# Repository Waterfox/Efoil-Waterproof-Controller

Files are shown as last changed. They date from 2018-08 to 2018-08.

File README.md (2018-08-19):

# Efoil-Waterproof-Controller

This repository contains everything you should need to build a waterproof controller for your electric hydrofoil

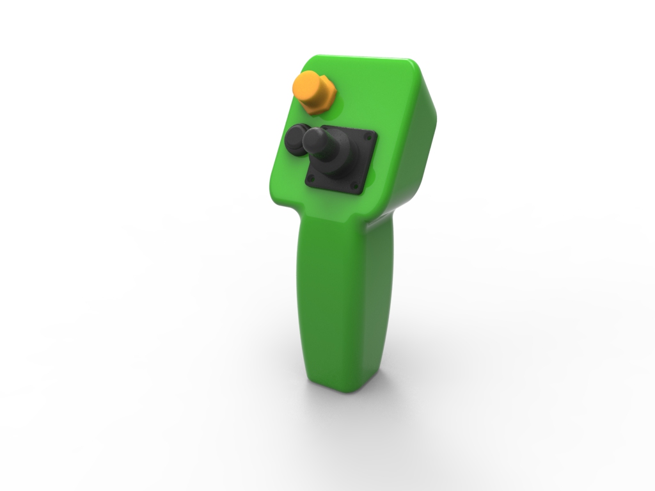
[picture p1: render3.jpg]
Controller Render


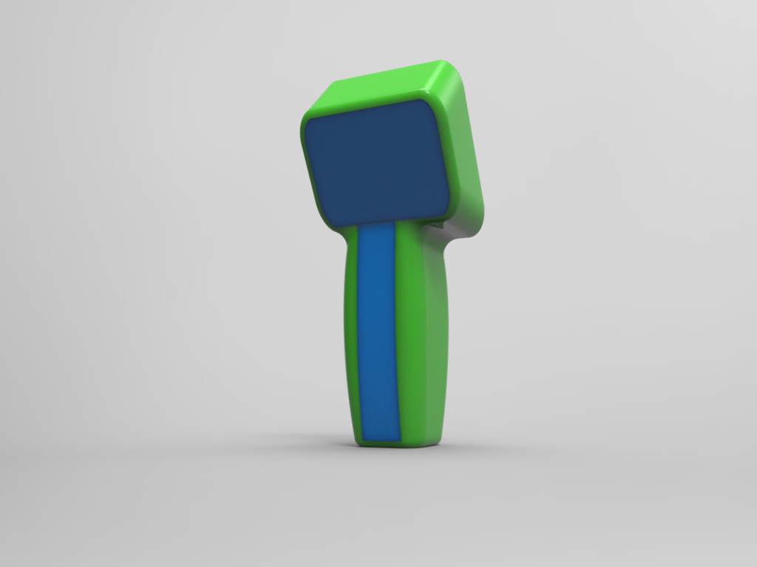
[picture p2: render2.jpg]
Controller Render


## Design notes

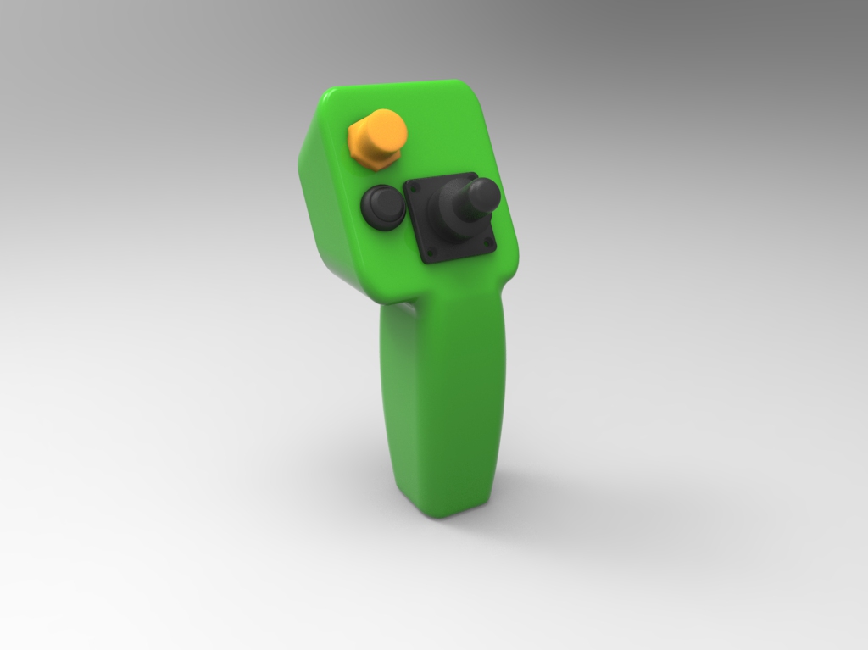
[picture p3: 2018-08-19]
render1.jpg

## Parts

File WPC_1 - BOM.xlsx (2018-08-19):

# | Part | Description | Manufacturer | Part number | Supplier | Supplier # | Quantity | Unit | CUR | Extended Cost | Website
1 | Joystick IP67 | SWITCH JOYSTICK FINGER TIP HALL | Grayhill | 67A-DF-3C-060C | Digikey | GH7700-ND (https://www.digikey.ca/product-detail/en/grayhill-inc/67A-DF-3C-060C/GH7700-ND/4360140) | 1 | 89 | CAD
2 | RF module - RX | SPARKFUN TRANSCEIVER BREAKOUT - SMA | Sparkfun | WRL-00705 | Digikey | 1568-1296-ND (https://www.digikey.ca/product-detail/en/sparkfun-electronics/WRL-00705/1568-1296-ND/5762446) | 1 | 28.41 | CAD
3 | RF module - TX | SPARKFUN TRANSCEIVER BREAKOUT - | Sparkfun | WRL-00691 | Digikey | 1568-1295-ND (https://www.digikey.ca/product-detail/en/sparkfun-electronics/WRL-00691/1568-1295-ND/5762445) | 1 | 28.41 | CAD
4 | Battery charger | SPARKFUN USB LIPOLY CHARGER - SI | Sparkfun | PRT-12711 | Digikey | 1568-1299-ND (https://www.digikey.ca/product-detail/en/sparkfun-electronics/PRT-12711/1568-1299-ND/5762449) | 1 | 21.29 | CAD
5 | Teensy MCU | DEV TEENSY 3.2 13736 | PJRC | DEV-13736 | Digikey | 1568-1231-ND | 2 | 31.6 | CAD
6 | ON/OFF but | SWITCH PUSHBUTTON SPST 4A 12V | APEM | IPR1SAD2L0G | Digikey | 679-1115-ND | 1 | 40.36 | CAD
7 | Charge port | Chogori Standard Series 4 POS Panel | Chogori | 22004535-01 |  |  |  |  |  |  | http://www.chogoriusa.com/standard.pdf
8 | Charge plug | Chogori Standard Series 4 POS Push Lock, Field installable | Chogori | 22004231-01
9 | USB A cable | USB A Cable
10 | 2 Part Urethane | Smooth-ON PMC 780 2 part Urethane |  |  |  |  |  |  |  |  | https://www.smooth-on.com/products/pmc-780-dry/
11 | Resistor 2K | I2C pullups, 2K-5K |  |  |  |  | 2
12 | Resistor 100 | Button LED, 100 Ohm |  |  |  |  | 1
13 | Battery | 1 cell from a Turnigy 3S 2200mAh LiPO | Hobbyking |  | HobbyKing | T2200.3S.20 | 1 | 8 | USD |  | https://hobbyking.com/en_us/turnigy-2200mah-3s-20c-lipo-pack.html
14 | M3 Screws | M3 X 5MM SHCS 18-8SS
15 | 5V reg | Regulate from your battery volage to 5V
WPC01 | 3D printed enclosure
WPC02 | 3D printed back panel 1
WPC03 | 3D printed back panel 2
WPC04 | controller assy

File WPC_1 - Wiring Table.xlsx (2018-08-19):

Waterproof Controller Basic Wiring
Waterproof Controller:
Teensy | NRF24L01 | Note
VIN | VCC | 4.2V from LIPO
GND | GND
D8 | IRQ
D9 | CE
D10 | CS
D11 | MOSI
D12 | MISO
D13 | SCK
 | Grayhill 67A
18 - SDA0 | 1 - SDA | Use pullup R to VIN or 3V3
3.3V | 2 - VDD
GND | 3 - VSS | GND
19 - SCL0 | 4 - SCL | Use pullup R to VIN or 3V3
D7 | 5 - INTn | connected but not used
 | 6 - A1n
 | Chogori Panel Connector
 | 1 | 5V Input from USB Charger
D- Pad | 2 | White wire USB
D+ Pad | 3 | Green wire USB
 | 4 | GND from USB Charger
 | Other
VIN | Pushbutton Switch from SF LiPo charger output
GND | SF LiPO charger output
Receiver:
Teensy | NRF24L01
VIN | VCC
GND | GND
D8 | IRQ
D9 | CE
D10 | CS
D11 | MOSI
D12 | MISO
D13 | SCK
 | Seaking 130A ESC
GND | BLACK
VIN | RED
D3 | White
 | 5V Reg
VIN | 5V REG '+ve'
GND | 5V REG GND

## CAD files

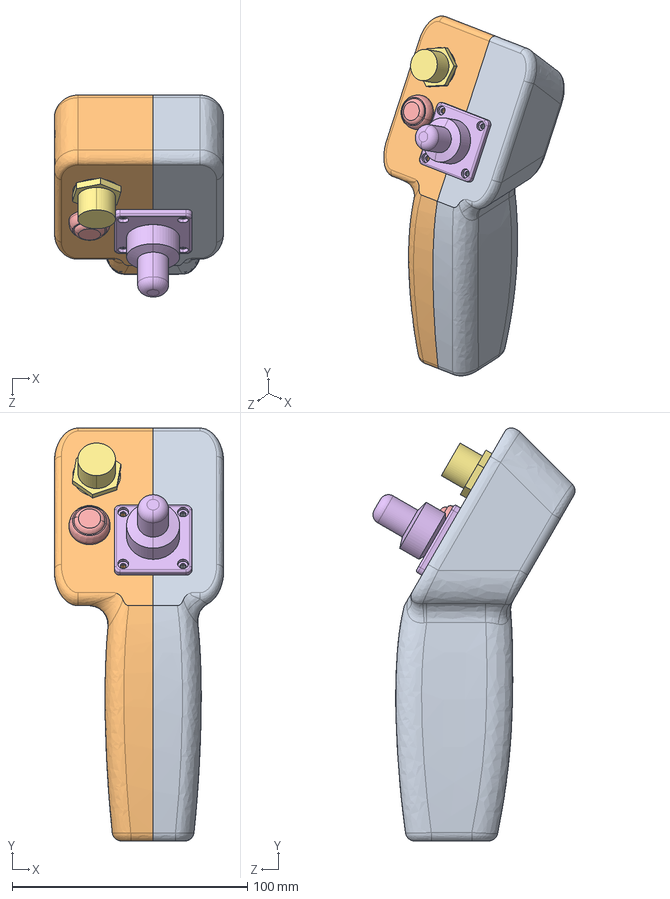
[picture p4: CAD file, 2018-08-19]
WPC04 - controller assy.STEP
72.0 x 175.4 x 85.8 mm
WPC01 - enclosure
2.6LipoFP
teensyFP
ApemPushbutton
grayhill67A
chogori fp
WPC03 - back cover2
WPC02 - back cover1

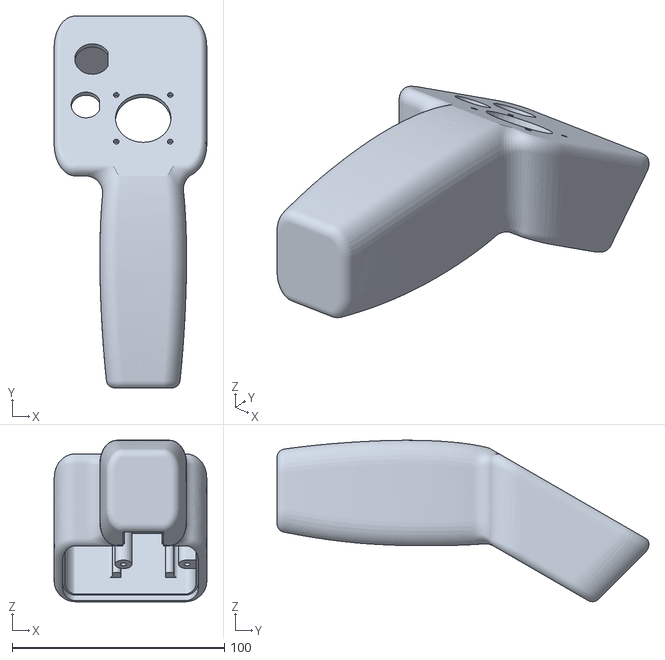
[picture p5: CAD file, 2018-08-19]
WPC01 - enclosure.STL
72.0 x 175.4 x 76.2

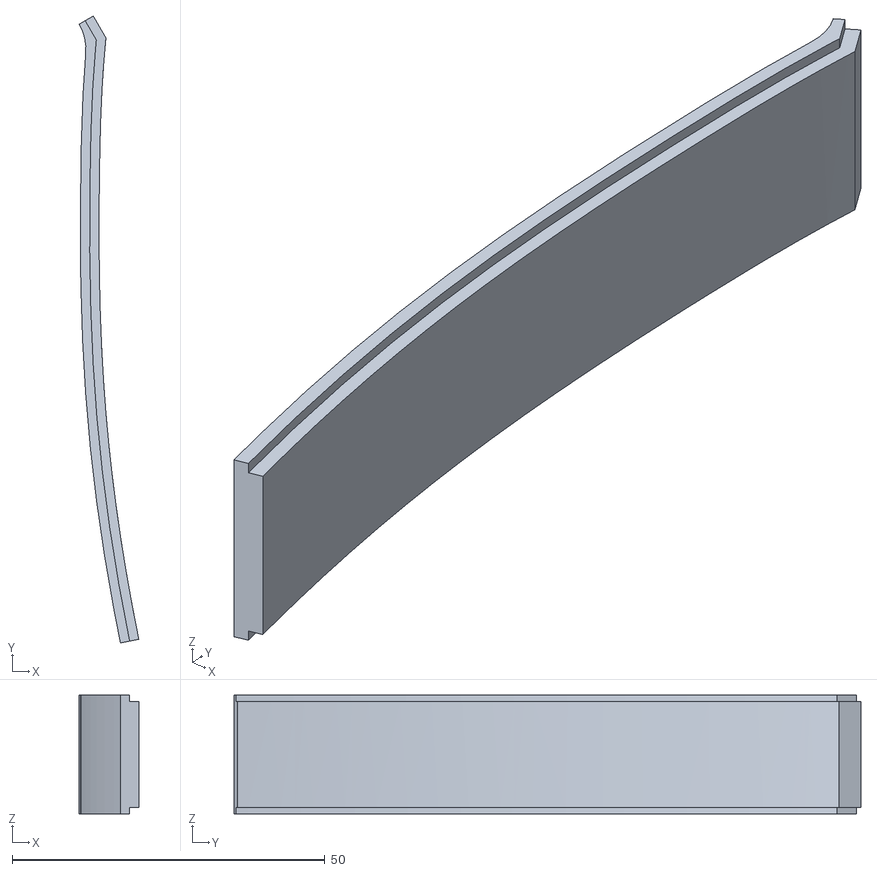
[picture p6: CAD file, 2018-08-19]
WPC03 - back cover2.STL
9.54 x 100.3 x 19.0

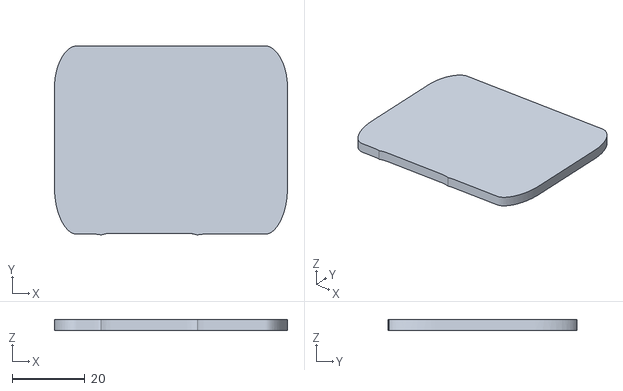
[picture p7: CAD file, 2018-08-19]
WPC02 - back cover1.STL
64.0 x 51.9 x 3.00

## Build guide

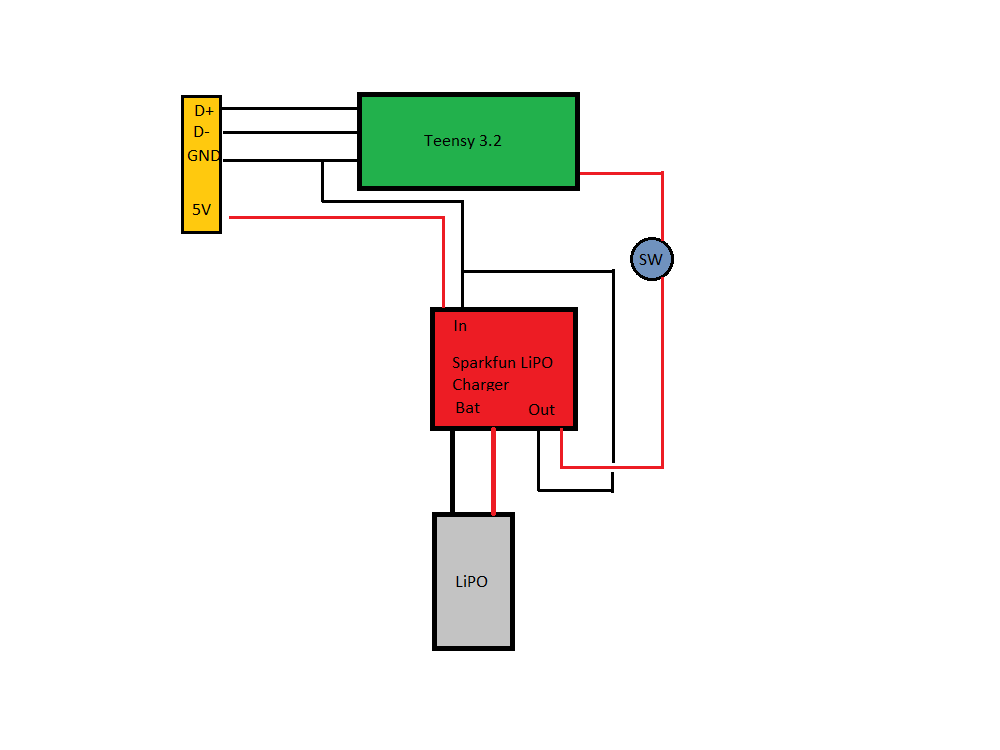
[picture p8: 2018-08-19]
bat charger wiring.png

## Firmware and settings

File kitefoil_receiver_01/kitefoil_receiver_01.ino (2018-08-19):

/* 
*  Wireless remote controller receiver with Grayhill 67A joystick and nRF24L01+ radios
*  Based on Teensy Examples
*  July 2018 Robbie Edwards
*/

#include <SPI.h>
#include <RF24.h>
#include <Servo.h>
#define THRUSTER_PIN 3

RF24 radio(9,10);
int xy[] = {0,0};
Servo m1;
int thruster_out = 90;
int missCount = 11;

byte addresses[][6] = {"1Node","2Node"};

void setup() {
  Serial.begin(115200);
  m1.attach(THRUSTER_PIN);
  radio.begin();
//  radio.setPALevel(RF_PA_LOW);
  radio.openReadingPipe(1,addresses[1]);
  radio.startListening();

}

void loop() {
  if (missCount > 10) thruster_out = 90; // If we don't receive anything for 10 cycles, set throttle to neutral
  if( radio.available()){
                                                                    
      while (radio.available()) {                                   
        radio.read( &xy, sizeof(xy) );             
      }
     
      Serial.print(xy[0]);Serial.print("  "); Serial.println(xy[1]);
      thruster_out = map(xy[1],-80,80,8,172);  // map the joystick output to the servo range
      missCount = 0;
   }
   else missCount = missCount + 1;

   if (thruster_out < 90) thruster_out = 90; // Don't allow reverse
   m1.write(thruster_out);
   delay(20);
}

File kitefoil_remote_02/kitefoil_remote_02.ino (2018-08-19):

/* 
*  Wireless remote controller with Grayhill 67A joystick and nRF24L01+ radios
*  Based on Teensy Examples
*  July 2018 Robbie Edwards
*/

#include <Wire.h>
#include <SPI.h>
#include <RF24.h>

//int led = LED_BUILTIN;
int x = 0;
int y = 0;
int xy[] = {0,0};

RF24 radio(9,10);
byte addresses[][6] = {"1Node","2Node"};

void setup()
{
//  pinMode(led, OUTPUT);
  Wire.begin();             // join i2c bus 
  Serial.begin(115200);       // start serial for output

  radio.begin();
//  radio.setPALevel(RF_PA_LOW);
  radio.openWritingPipe(addresses[1]);
  radio.openReadingPipe(1,addresses[0]);
  
}

void loop()
{


//  digitalWrite(led, HIGH);  // briefly flash the LED
  //Read from the Grayhill 67A Joystick
  xy[0] = 0;
  xy[1] = 0;
  Wire.requestFrom(0x40, 2);   // 7 bit address, the read / write bit is appended by Wire lib
  if (Wire.available()) { // slave may send less than requested
    int c = Wire.read();   // receive a byte as character
    if (c >127) xy[0] = c - 256;
    else xy[0] = c;
  }
  if (Wire.available()) { // slave may send less than requested
    int c = Wire.read();   // receive a byte as character
    if (c >127) xy[1] = c - 256;
    else xy[1] = c;
  }
    
  Serial.print(xy[0]);Serial.print("  "); Serial.println(xy[1]);

  if (!radio.write( xy, sizeof(xy) )){
       Serial.println(F("failed"));
  }
  

  
//  digitalWrite(led, LOW);
  delay(20);
}
